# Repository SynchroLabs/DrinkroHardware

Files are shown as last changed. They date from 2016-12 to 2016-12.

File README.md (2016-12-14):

#Introduction

This is a controller board with two L293D H-Bridge ICs used to run four DC
motors. In my application I used a 12VDC power supply and four 12VDC
peristaltic pumps for pumping drink ingredients.

The master branch of this repo may not be completely tested and ready to
produce. For a stable version, look at the release tags.

We are using this board in conjunction with a [Raspberry Pi 3 Model
B](https://www.raspberrypi.org/products/raspberry-pi-3-model-b/) and iOS,
Android, Windows Phone and Windows [drink
software](https://github.com/SynchroLabs/Drynkro) built with the [Synchro
platform](https://synchro.io).

#Hooking Things Up

The motors are hooked up to `J11`-`J14`. Plug in a DC power supply to `J1`.

Note that each motor can draw up to 300mA, so make sure that your DC power
supply can handle it if you want to drive more than one motor at a time.

Connect `J10` to a Raspberry Pi / Arduino / whatever you want as a controller.
Provide `VCCIO`, this must match your controller GPIO voltage, and connect
`GND`. `MOTOR1_EN` etc. are the motor enable lines, and can be PWM controlled
for speed control, or hooked up to regular GPIOs. I have not done a lot of
testing with speed control, I just turn the motors completely on and off with a
regular GPIO. The motor control lines have a pulldown resistor -- if these are
not installed, then the motor may default to enabled, depending on the L293D
chip you use. I'm using the ST Micro version and this was the case for that
chip.

`J2`-`J9` are used for motor direction. Each header has a VCCIO and a GND pin.
`DIR1` and `DIR2` must be set to opposite values -- that is, set `J2`
(`MOTOR1_DIR1`) to jumper to `VCCIO`, then set `J3` (`MOTOR1_DIR2`) to jumper
to `GND`. See the L293D datasheet for more information about how this works
internally in the chip. If the motor is running the wrong direction (pumping
the wrong way in my case), then swap both jumpers. If you want, you can skip
the jumpers and drive the direction pins directly from your controller.
However, there are no pullups or pulldowns on the lines, so be careful about
enabling a motor with the direction pins floating. I use jumpers in my case as
I don't care to run the pumps in reverse.

#Other Stuff

This is a good writeup on version control and EAGLE

https://spin.atomicobject.com/2015/01/19/hardware-version-control/

Some design considerations surround the current on VCC. Each motor can draw up
to 600mA, so the total current on VCC can be up to 2.4A (all four motors
running). Using the calculator at http://www.4pcb.com/trace-width-calculator.html
you need to make sure the trace width is suitable. The minimum trace for 2.4A
on 1oz copper is ~40mil.

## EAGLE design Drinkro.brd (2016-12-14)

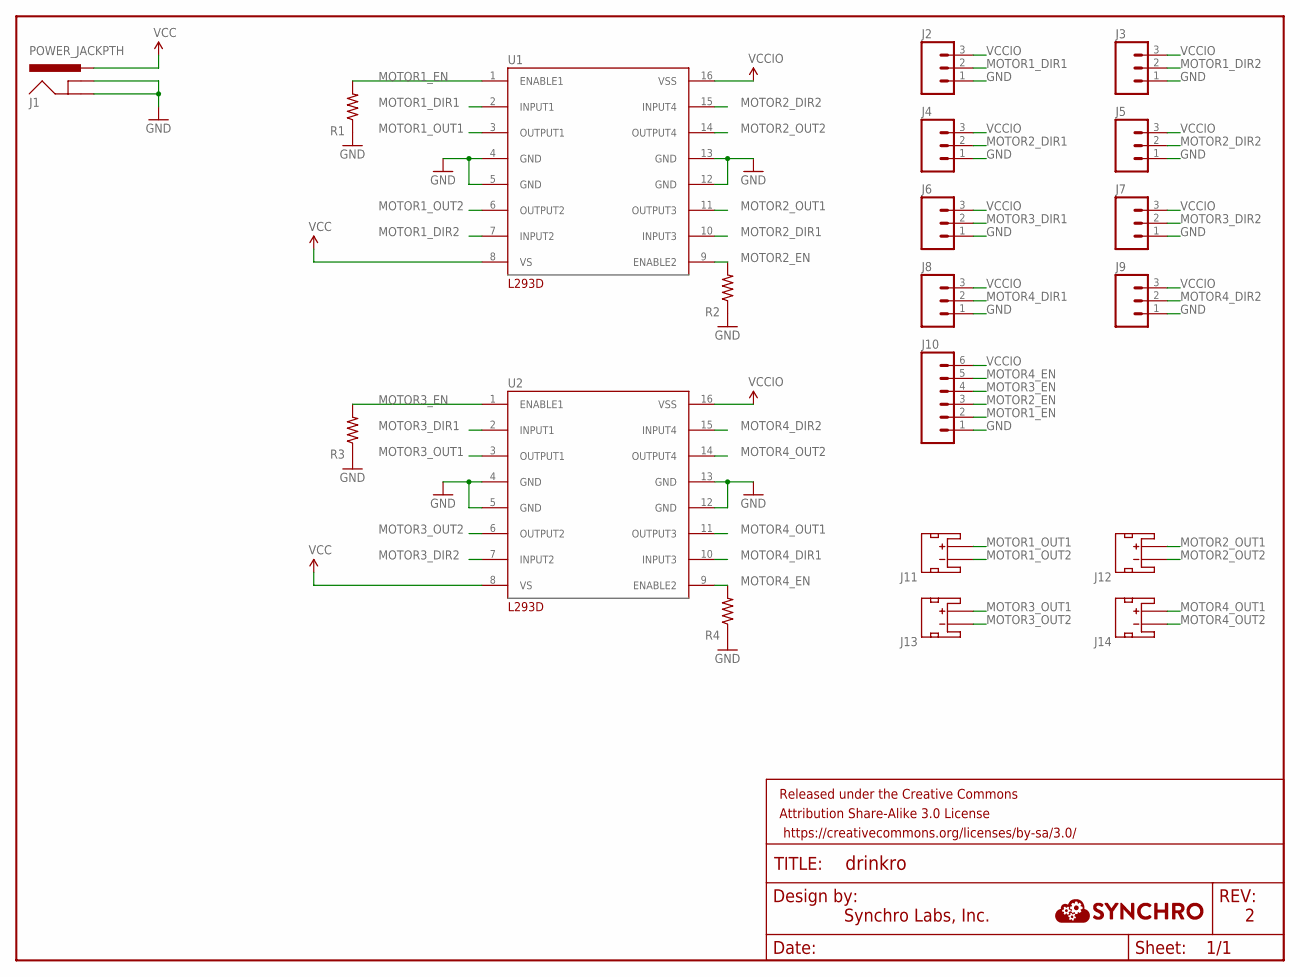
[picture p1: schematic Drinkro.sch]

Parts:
FRAME1: FRAME-LETTER; CREATIVE_COMMONS
J1: POWER_JACKPTH; POWER_JACK_PTH
J2, J3, J4, J5, J6, J7, J8, J9: M03PTH; 1X03
J10: M06SILK_FEMALE_PTH; 1X06
J11, J12, J13, J14: JST_2MM_MALE; JST-2-SMD
R1, R2, R3, R4: RESISTOR0805-RES; 0805
U1, U2: L293D; DIP

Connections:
GND: J1.GND, J1.GNDBREAK, J2.1, J3.1, J4.1, J5.1, J6.1, J7.1, J8.1, J9.1, J10.1, R1.1, R2.1, R3.1, R4.1, U1.4 (GND), U1.5 (GND), U1.12 (GND), U1.13 (GND), U2.4 (GND), U2.5 (GND), U2.12 (GND), U2.13 (GND)
MOTOR1_DIR1: J2.2, U1.2 (INPUT1)
MOTOR1_DIR2: J3.2, U1.7 (INPUT2)
MOTOR1_EN: J10.2, R1.2, U1.1 (ENABLE1)
MOTOR1_OUT1: J11.2 (+), U1.3 (OUTPUT1)
MOTOR1_OUT2: J11.1 (-), U1.6 (OUTPUT2)
MOTOR2_DIR1: J4.2, U1.10 (INPUT3)
MOTOR2_DIR2: J5.2, U1.15 (INPUT4)
MOTOR2_EN: J10.3, R2.2, U1.9 (ENABLE2)
MOTOR2_OUT1: J12.2 (+), U1.11 (OUTPUT3)
MOTOR2_OUT2: J12.1 (-), U1.14 (OUTPUT4)
MOTOR3_DIR1: J6.2, U2.2 (INPUT1)
MOTOR3_DIR2: J7.2, U2.7 (INPUT2)
MOTOR3_EN: J10.4, R3.2, U2.1 (ENABLE1)
MOTOR3_OUT1: J13.2 (+), U2.3 (OUTPUT1)
MOTOR3_OUT2: J13.1 (-), U2.6 (OUTPUT2)
MOTOR4_DIR1: J8.2, U2.10 (INPUT3)
MOTOR4_DIR2: J9.2, U2.15 (INPUT4)
MOTOR4_EN: J10.5, R4.2, U2.9 (ENABLE2)
MOTOR4_OUT1: J14.2 (+), U2.11 (OUTPUT3)
MOTOR4_OUT2: J14.1 (-), U2.14 (OUTPUT4)
VCC: J1.PWR, U1.8 (VS), U2.8 (VS)
VCCIO: J2.3, J3.3, J4.3, J5.3, J6.3, J7.3, J8.3, J9.3, J10.6, U1.16 (VSS), U2.16 (VSS)

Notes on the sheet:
Synchro Labs, Inc.

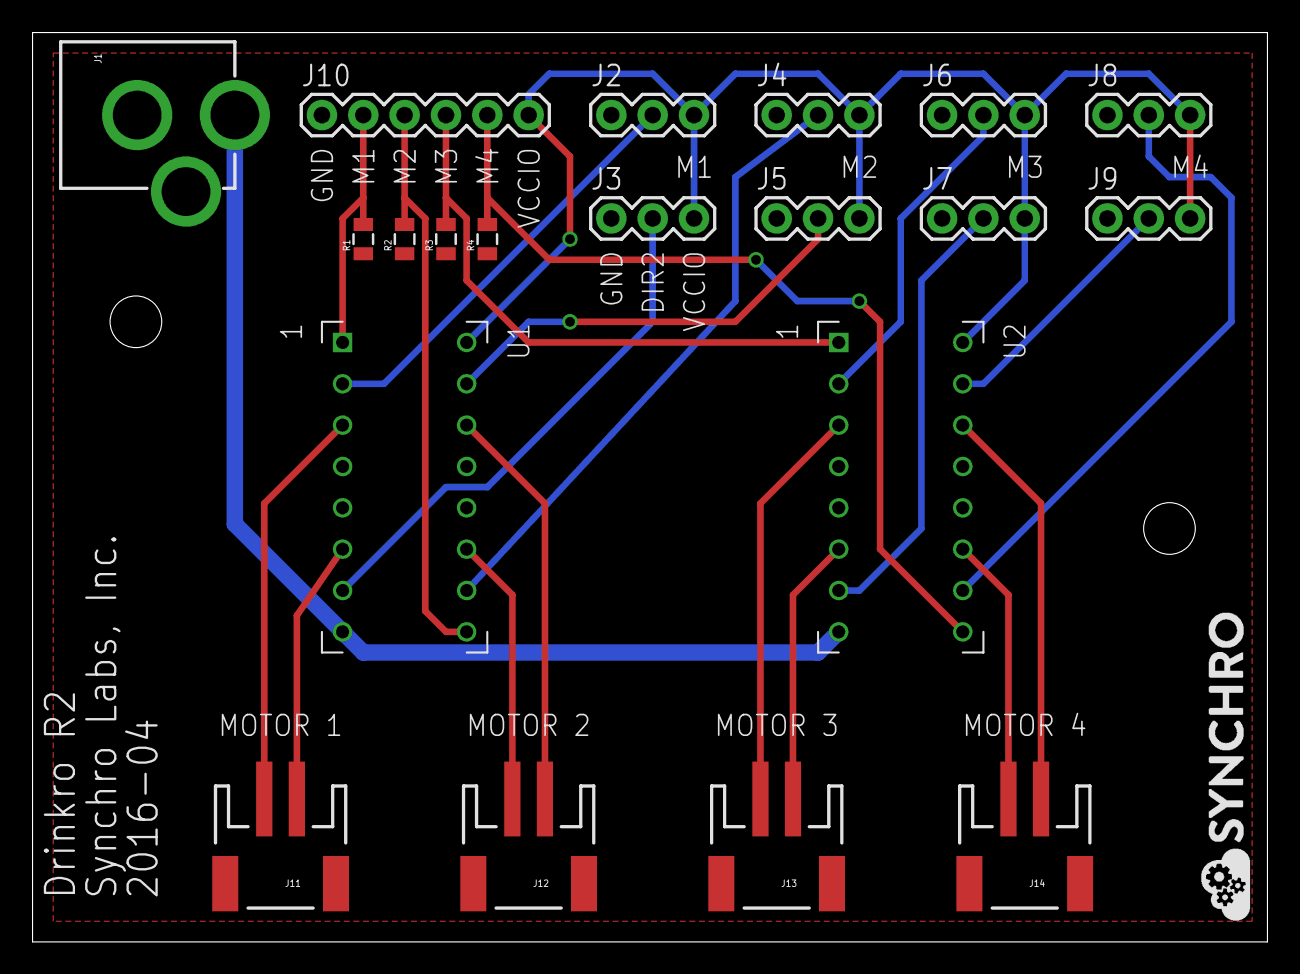
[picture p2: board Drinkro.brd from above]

Board: 2 copper layers, 75.9 x 55.9 mm, 21 parts (0 on the bottom side), 23 nets.

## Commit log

2016-05-01 R1 final board.
    [Drinkro.brd, Drinkro.sch]
2016-05-01 First cut of .gitignore.
2016-05-01 Added revision and company.
    [Drinkro.sch]
2016-05-02 Silkscreen changes. Revision bump to 2.
    [Drinkro.brd, Drinkro.sch]
2016-05-02 Increased wire width on VCC and added mounting holes.
    [Drinkro.brd]
2016-05-04 Added logo.
    [Drinkro.brd]
2016-05-04 Cleaned up MOTOR1_OUT1 routing.
    [Drinkro.brd]
2016-05-04 Added logo to schematic.
    [Drinkro.sch]
2016-05-20 Changed mounting hole size.
    [Drinkro.brd]
2016-12-14 Fixed some text alignment, new Eagle version.
    [Drinkro.brd]

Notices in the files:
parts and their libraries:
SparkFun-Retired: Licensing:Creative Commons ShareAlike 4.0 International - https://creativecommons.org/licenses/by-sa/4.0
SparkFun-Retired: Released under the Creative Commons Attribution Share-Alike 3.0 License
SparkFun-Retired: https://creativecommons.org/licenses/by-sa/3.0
